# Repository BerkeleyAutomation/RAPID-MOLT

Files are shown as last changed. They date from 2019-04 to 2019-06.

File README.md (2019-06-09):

## RAPID-MOLT: A Meso-scale, Open-source, Low-cost Testbed for Robot Assisted Precision Irrigation and Delivery

To study the automation of plant-level precision irrigation, we present a modular, open-source testbed that enables real-time, fine-grained data collection and irrigation actuation. RAPID-MOLT costs USD $610 and is sized to fit a small laboratory floor space of 0.37 m^2. The functionality of the platform is evaluated by measuring the correlation between plant growth (Leaf Area Index) and water stress (Crop Water Stress Index) with irrigation volume. In line with biological studies, the observed plant growth is positively correlated with irrigation volume while water stress is negatively correlated. This testbed is the basis for ongoing work on learning-based irrigation controllers. 

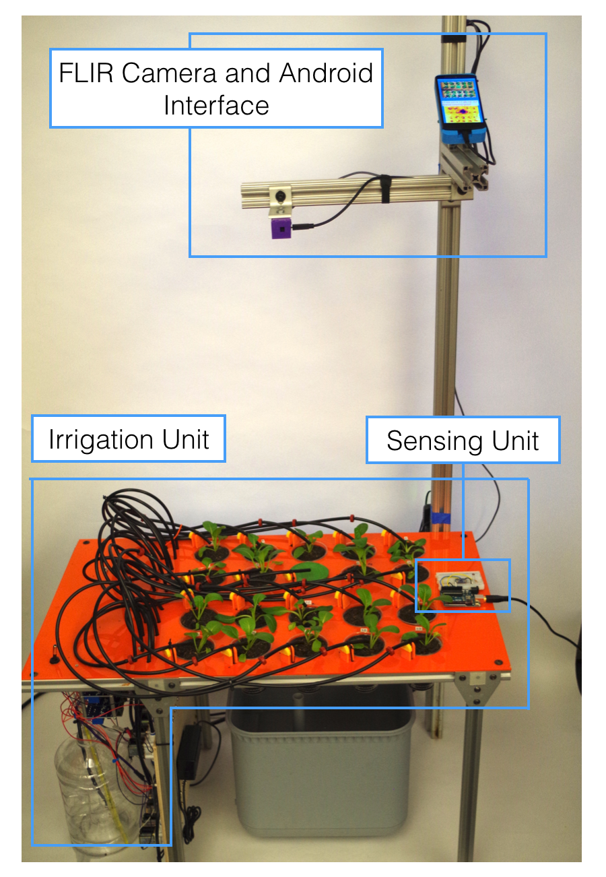
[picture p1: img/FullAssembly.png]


## Platform Basics
The contributions are as follows:
1. A hardware system design that enables both plant level sensing with multispectral imaging and also precise irrigation control with Raspberry Pi actuated solenoids.
2. A software infrastructure and data processing pipeline to evaluate irrigation controllers, including the automatic extraction of Leaf Area Index and Crop Water Stress Index from RGB and thermal images.
3. Experimental data from two experiments with different crops, reflecting plant growth and water stress data in response to different irrigation schedules.

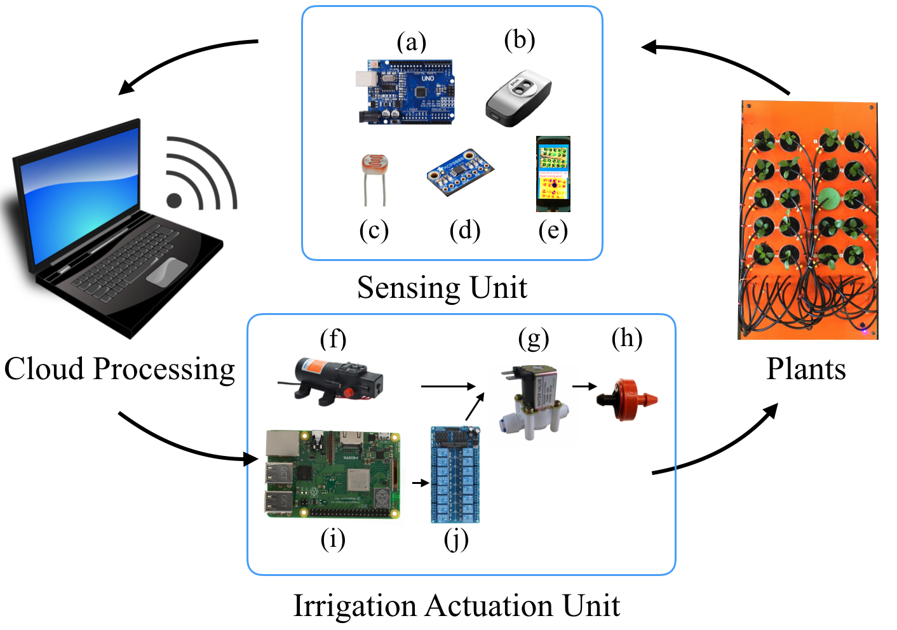
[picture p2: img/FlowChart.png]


As seen in the flow chart above, each platform unit functions together as follows. Plant and environmental images and data are collected by the sensing unit, and sent to the cloud processing unit for the creation of data-specific irrigation schedules. These schedules are relayed to the irrigation unit for irrigation deployment to the potted plants.

## Software

The software is grouped in 1) sensing, 2) data processing, and 3) actuation. 
1) The sensing folder contains the code for the android app (uploades the thermal and rgb images to the cloud) and the arduino uno. 
2) The data processing contains two core files:
- downloadImagesFromGoogleDrive.py    downloads the images from the cloud to the local computer
- process_images.py                   extracts the LAI and leaf temperature out of the images
3) The actuation folder contains the scripts and files for the raspberry pie to execute the derived irrigation schedule.

The Data folder contains an example of images from one experiment and the files resulting from the image processing.

## Hardware
CAD models for construction can be found on this repository. Code for the software infrastructure and experimental data will be posted soon.

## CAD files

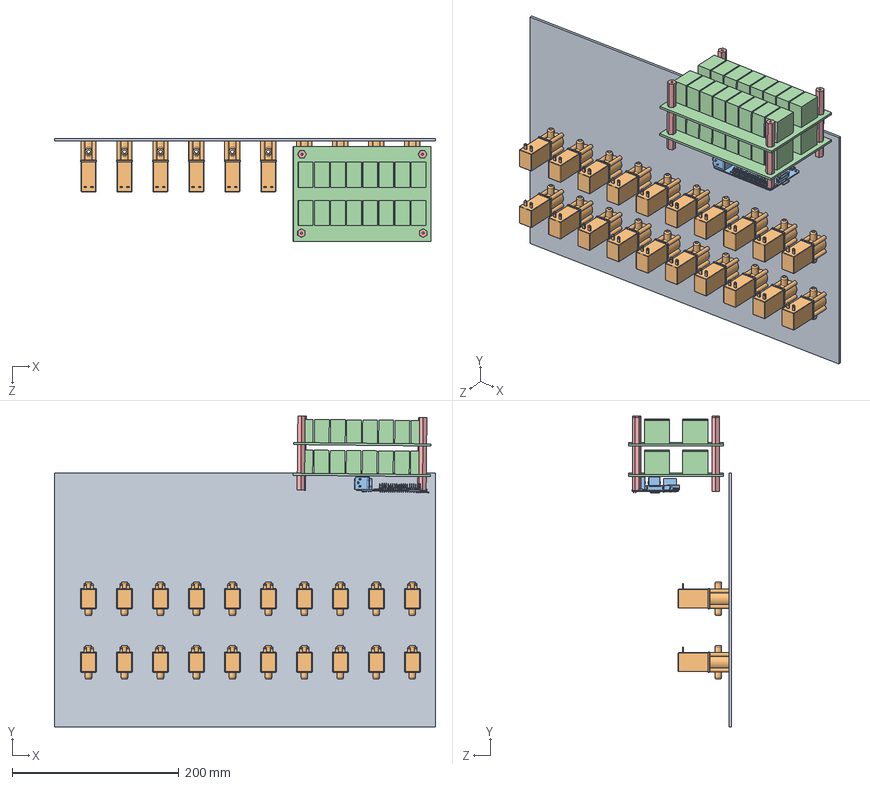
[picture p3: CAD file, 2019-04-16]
CAD/Sample Side Mount Assembly for Fusion.SLDASM
457.2 x 373.0 x 123.8 mm
Side Mount Plate
solenoid x 20
Raspberry Pi 3 Light Version
Relay_16 x 2
hex_bars x 4

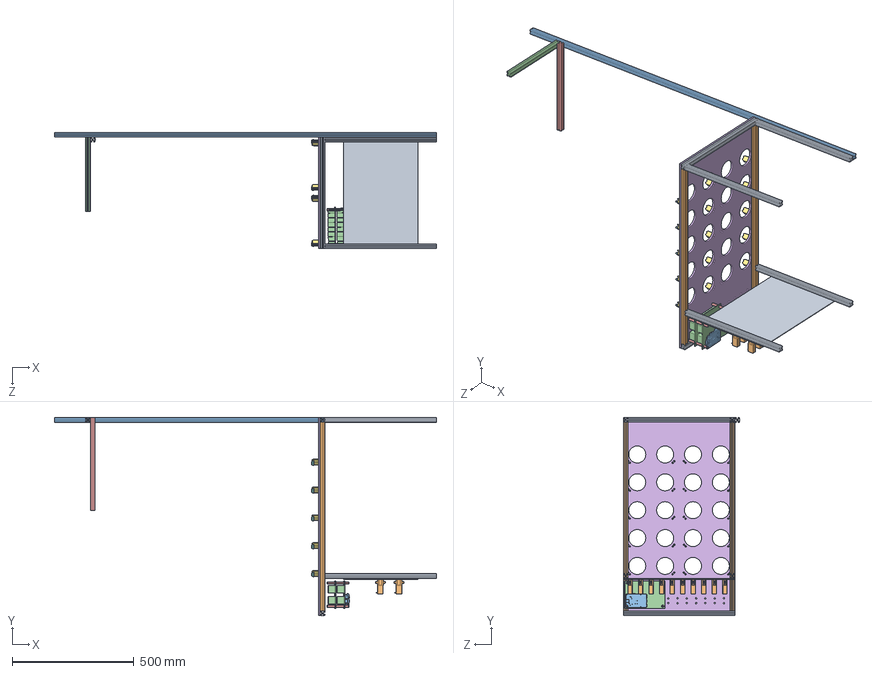
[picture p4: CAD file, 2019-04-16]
CAD/testbed_assem_3_13.SLDASM
1567.2 x 813.7 x 477.2 mm
20_2020_457_2_CL x 6
773.68_v3 x 2
1567.18_Mount8020
12in_mount
15in_Mount
top_plate
tube support x 20
add on 4 x 20
Side Mount Plate
solenoid x 20
Raspberry Pi 3 Light Version
Relay_16 x 2
hex_bars x 4

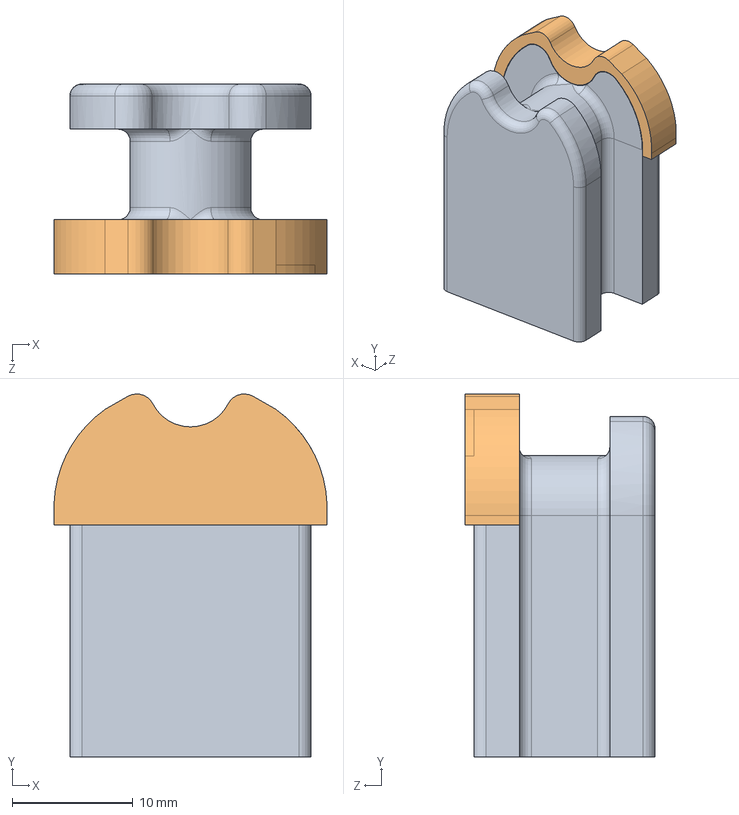
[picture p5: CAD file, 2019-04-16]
CAD/raiser assembly 2.SLDASM
22.6 x 30.1 x 15.8 mm
tube support
add on 4

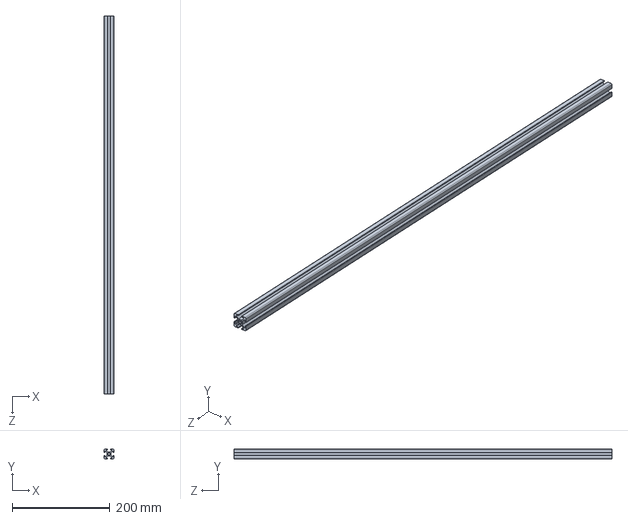
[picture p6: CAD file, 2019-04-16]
CAD/773.68_v3.SLDPRT
20.0 x 20.0 x 773.7 mm

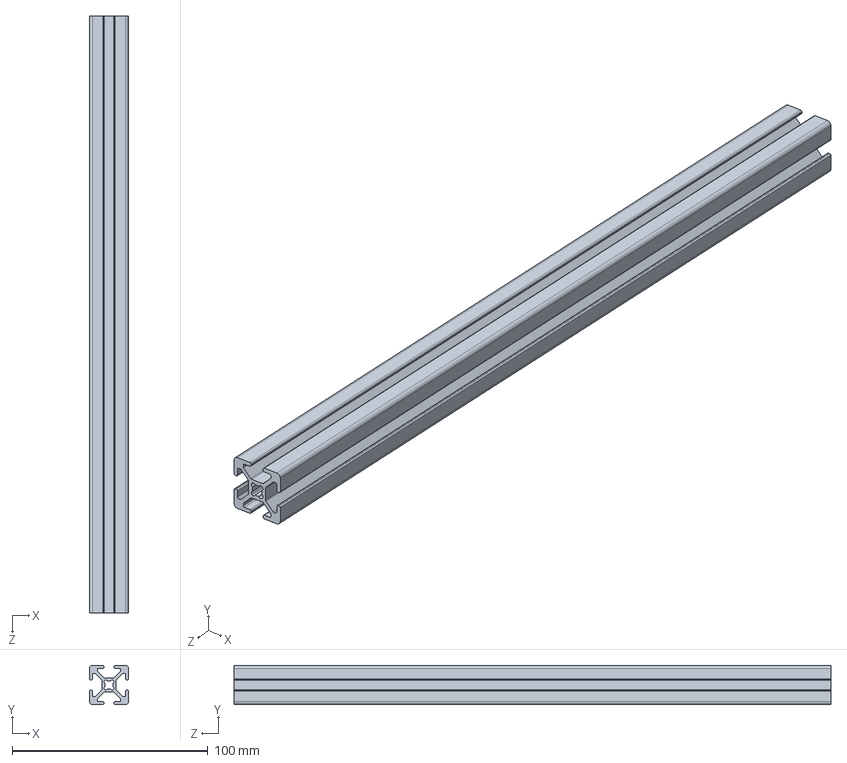
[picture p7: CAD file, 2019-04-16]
CAD/12in_mount.SLDPRT
20.0 x 20.0 x 304.8 mm

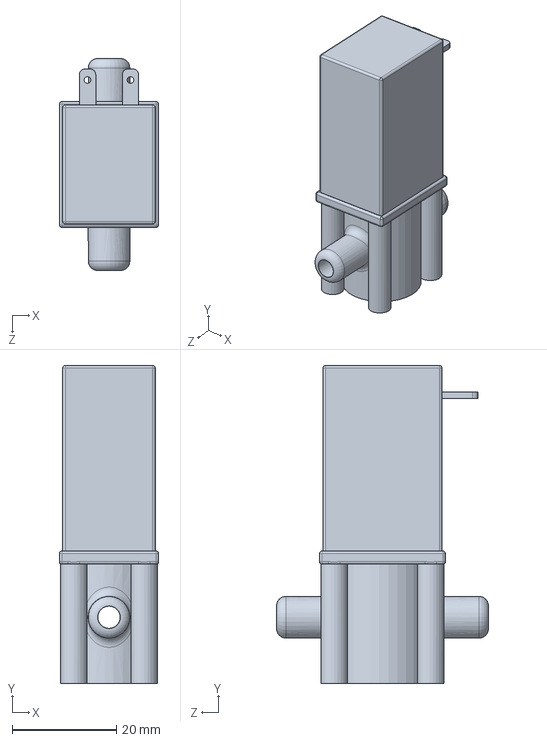
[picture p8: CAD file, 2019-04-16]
CAD/solenoid.SLDPRT
19.1 x 61.0 x 40.6 mm

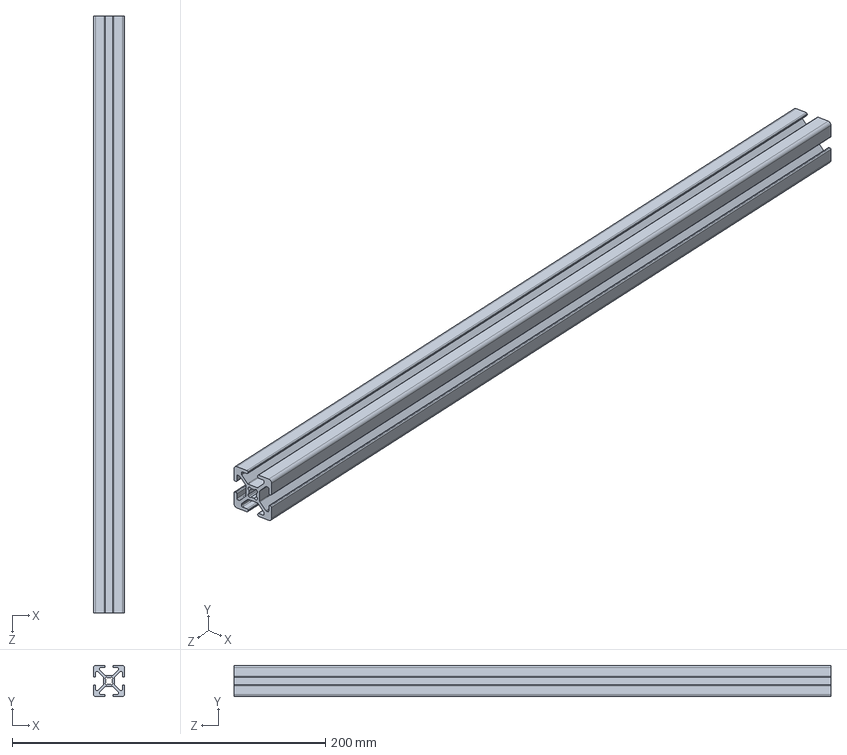
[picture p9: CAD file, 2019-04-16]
CAD/15in_Mount.SLDPRT
20.0 x 20.0 x 381.0 mm

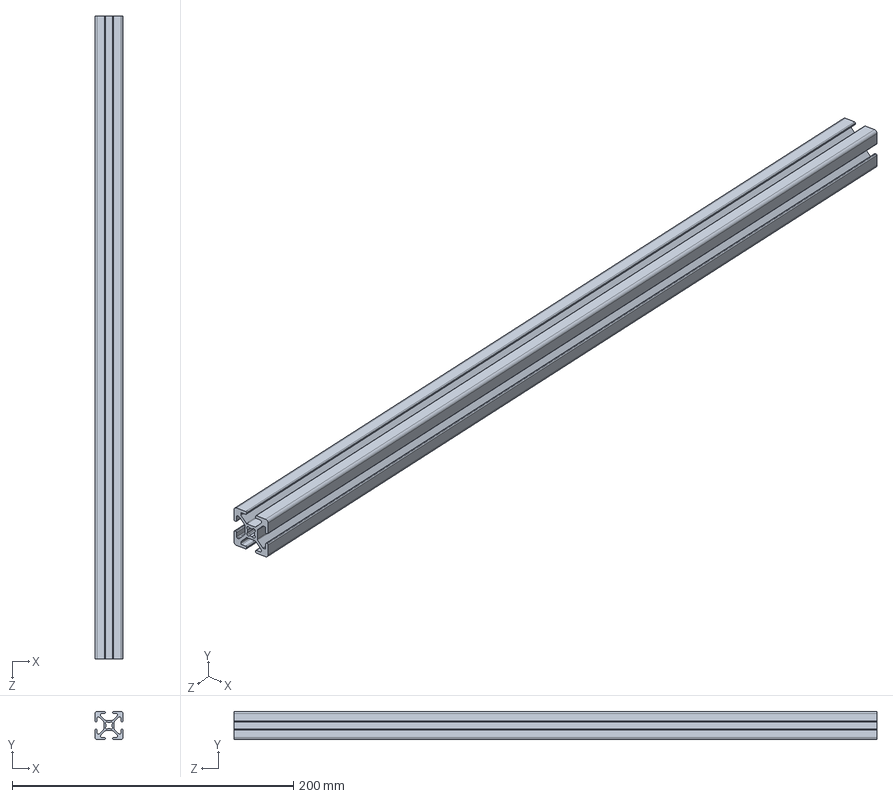
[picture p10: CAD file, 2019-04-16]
CAD/20_2020_457_2_CL.sldprt
20.0 x 20.0 x 457.2 mm

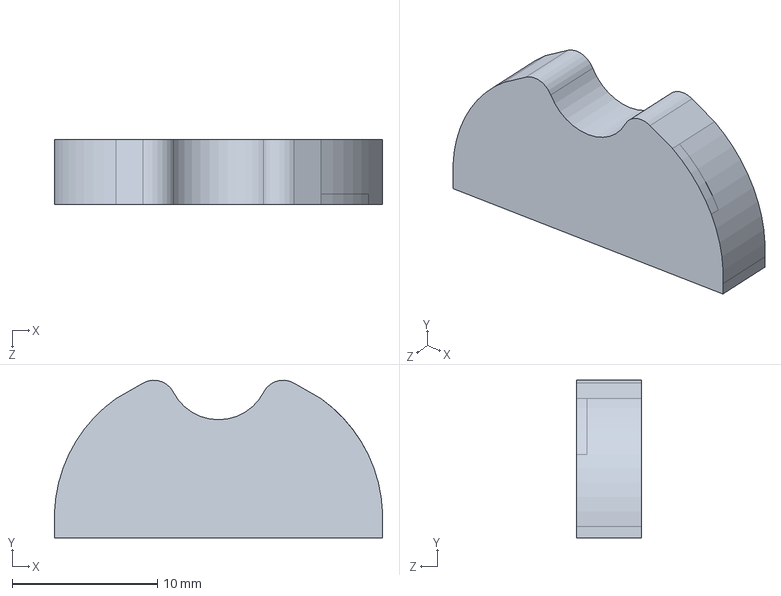
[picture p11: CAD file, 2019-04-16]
CAD/add on 4.SLDPRT
22.6 x 10.9 x 4.50 mm

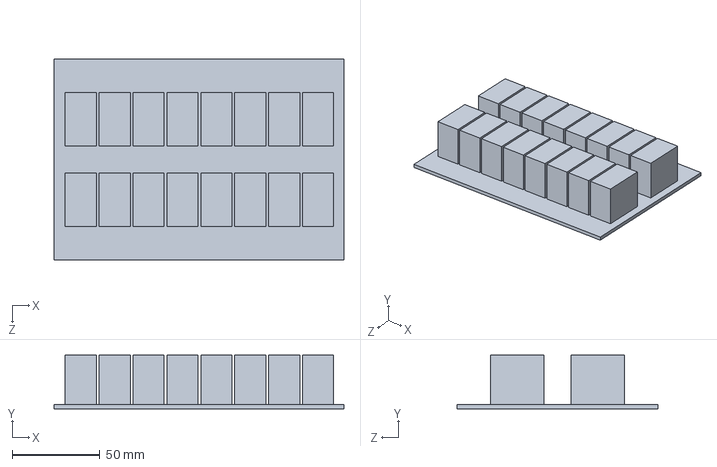
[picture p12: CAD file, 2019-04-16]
CAD/Relay_16.SLDPRT
165.1 x 30.5 x 114.3 mm

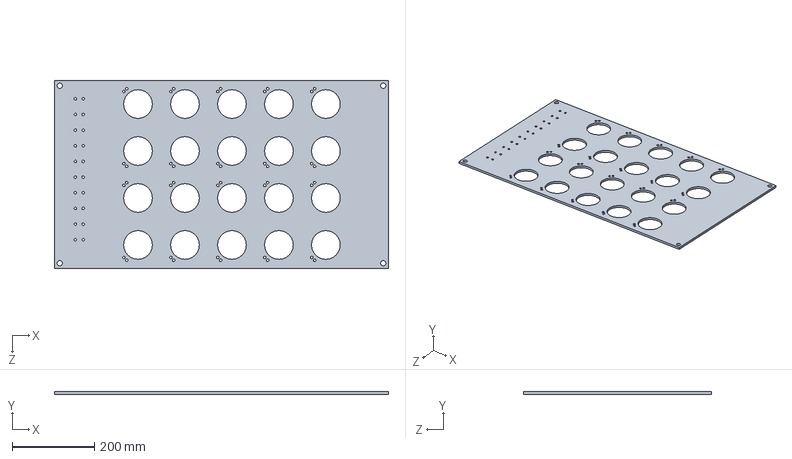
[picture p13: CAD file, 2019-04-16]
CAD/top_plate.SLDPRT
812.8 x 6.35 x 457.2 mm

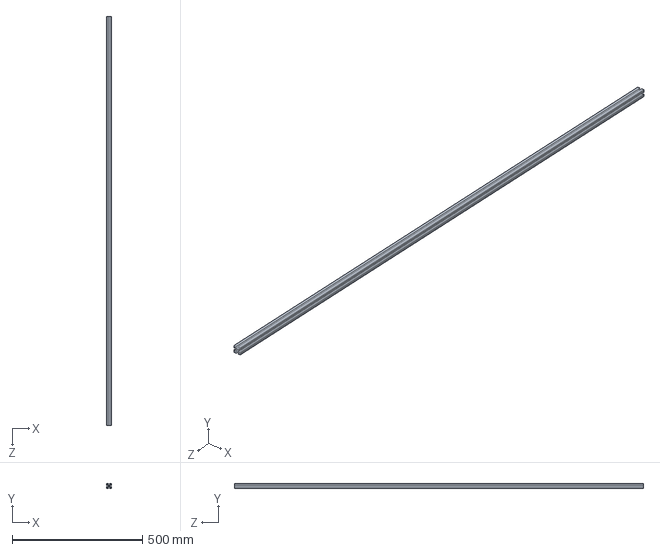
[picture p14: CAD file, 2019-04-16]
CAD/1567.18_Mount8020.SLDPRT
20.0 x 20.0 x 1567.2 mm

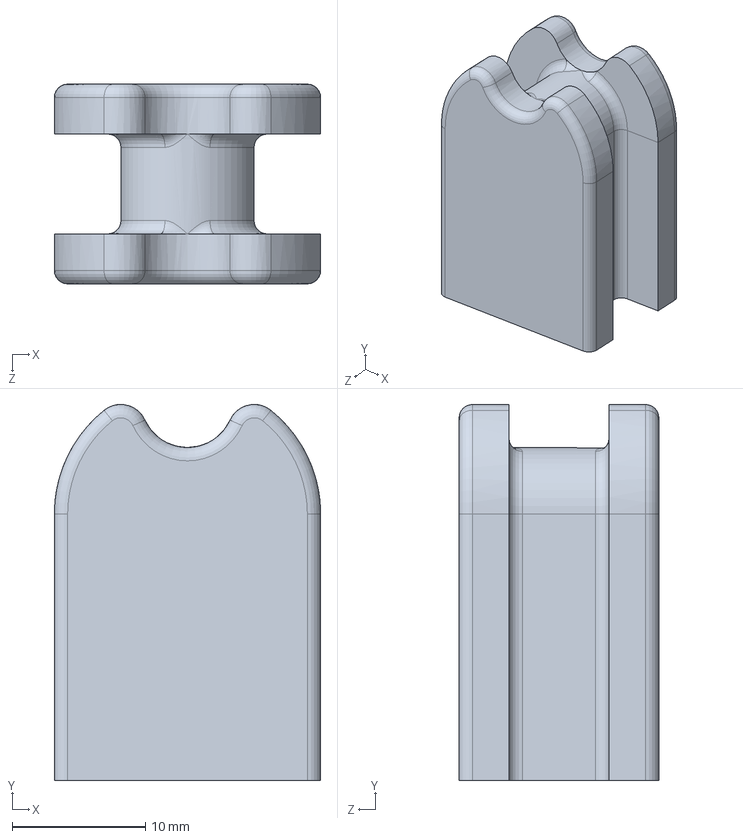
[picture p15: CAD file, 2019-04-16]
CAD/tube support.SLDPRT
20.0 x 28.2 x 15.0 mm

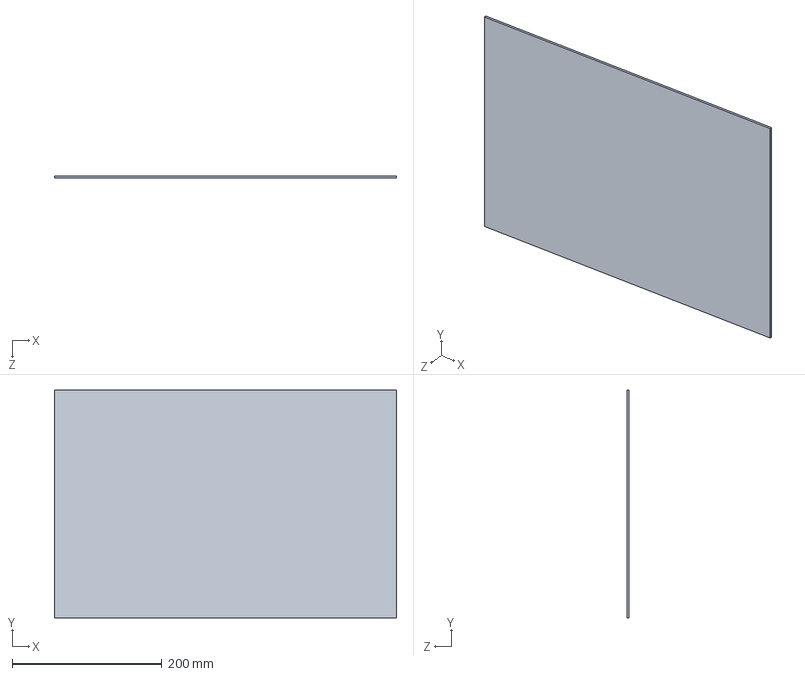
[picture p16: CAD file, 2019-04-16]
CAD/Side Mount Plate.SLDPRT
457.2 x 304.8 x 3.17 mm

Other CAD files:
CAD/hex_bars.SLDPRT

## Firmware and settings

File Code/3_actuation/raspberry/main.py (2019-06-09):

'''
This is the main script, running on the raspberry pie to control the irrigation actuation via the solenoids.

It reads from:
- emitterPinout.csv
- irrigationSchedule.csv

Format in irrigation Schedule.csv:
<pinout>, <hour>, <minute>, <second>, irrigated today (1 is yes, 0 is no)

The script logs every opening of a solenoid to: irrigationLog.txt
'''

import csv
import numpy as np
from time import sleep
import datetime
import RPi.GPIO as GPIO

irrigationSchedule = np.zeros((20, 5))
GPIO_pinout = np.zeros((20, 2))
killAll = False

# path where the irrigation log is saved
path = '/home/pi/Desktop/'
desktop_path = '/home/pi/Desktop/'
# path to the irrigation file
irrigation_file = 'irrigationSchedule.csv'

# settings for the Wet Area Reference Surface:
# Port:
wet_cloth_pot = 12
# the rate after which it should be irrigated in minutes
wet_cloth_rate = 30

GPIO.setwarnings(False)
GPIO.setmode(GPIO.BOARD)


def OnShutdown():
    global killAll
    killAll = True


def openEmitter(emitterNum, duration):
    # GPIO pin 40 is the water pump
    global GPIO_pinout
    GPIO.setup(40, GPIO.OUT)
    sleep(1)
    GPIO.output(40, GPIO.LOW)

    GPIO.setup(int(GPIO_pinout[emitterNum, 1]), GPIO.OUT)
    print('emitter number ', str(emitterNum), ' is open')
    GPIO.output(int(GPIO_pinout[emitterNum, 1]), GPIO.LOW)
    sleep(duration)
    GPIO.output(int(GPIO_pinout[emitterNum, 1]), GPIO.HIGH)

    GPIO.output(40, GPIO.HIGH)
    print('emitter number ', str(emitterNum), ' is close')

    # write to log file
    f = open(desktop_path+'irrigationLog.txt', 'a+')
    date = datetime.datetime.now().date()
    time = datetime.datetime.now().time()
    f.write(str(date) + ' ' + str(time) + ' ' + 'emitter num: ' + str(emitterNum) + ' '
            + 'duration: ' + str(duration) + '\r\n')
    f.close()


def main():
    # global irrigationSchedule
    global killAll
    global GPIO_pinout
    killAll = False

    # set the current date
    date = datetime.datetime.now().date()
    previous_day = (date - datetime.timedelta(days=1)).day
    last_time_cloth_watered = datetime.datetime.now() - datetime.timedelta(minutes=30)
    
    # read and update pinout
    from_txt = np.genfromtxt(path+'emitterPinout.csv', delimiter=',')
    for row in range(0, 20, 1):
        for col in range(0, 2, 1):
            GPIO_pinout[row, col] = int(from_txt[row, col])
    
    # closing all emitter
    for i in range(0, 20 ,1):
       GPIO.setup(int(GPIO_pinout[i, 1]), GPIO.OUT)
       GPIO.output(int(GPIO_pinout[i, 1]), GPIO.HIGH)
    sleep(2)

    # constant loop
    while ~killAll:
        # update irrigationSchedule
        from_txt = np.genfromtxt(path+irrigation_file, delimiter=',')
        for row in range(0, 20, 1):
            for col in range(0, 5, 1):
                irrigationSchedule[row, col] = from_txt[row, col]

        # check if the day changed, if yes updated irrigation status
        date = datetime.datetime.now().date()
        if date.day != previous_day:
            print('day changed, initializing irrigation status...')
            # initializing the irrigation tracking
            for row in irrigationSchedule:
                irrigationSchedule[int(row[0]), 4] = 0
                with open(path+irrigation_file, 'wb') as cvsfile:
                    to_txt = csv.writer(cvsfile, delimiter=',')
                    for row in irrigationSchedule:
                        to_txt.writerow(row)
            previous_day = date.day

        # check if the wet cloth should be irrigated again
        if datetime.datetime.now() >= (last_time_cloth_watered + datetime.timedelta(minutes=wet_cloth_rate)):
                # set the irrigation schedule at wet cloth pot to "not irrigated"
                irrigationSchedule[wet_cloth_pot, 4] = 0
                # Write it to the CSV file
                with open(path+irrigation_file, 'wb') as cvsfile:
                    to_txt = csv.writer(cvsfile, delimiter=',')
                    for row in irrigationSchedule:
                        to_txt.writerow(row)
                # set last_time_cloth_watered to current
                last_time_cloth_watered = datetime.datetime.now()

        time_now = datetime.datetime.now().time()
        time_now_int = int(time_now.hour * 60 + time_now.minute)

        # iterate over the schedule and open corresponding emitters
        for row in irrigationSchedule:
            emitter_num = int(row[0])
            irrigation_hour = row[1]
            irrigation_minute = row[2]
            irrigation_duration = row[3]
            was_irrigated = row[4]

            # check which emitters should be open and open them
            if time_now_int > (irrigation_hour*60+irrigation_minute) and was_irrigated == 0:
                irrigationSchedule[emitter_num, 4] = 1
                with open(path + irrigation_file, 'wb') as cvsfile:
                    to_txt = csv.writer(cvsfile, delimiter=',')
                    for row in irrigationSchedule:
                        to_txt.writerow(row)
                openEmitter(emitter_num, irrigation_duration)

        sleep(2)

if __name__ == '__main__':
    try:
        main()
    except KeyboardInterrupt:
        OnShutdown()

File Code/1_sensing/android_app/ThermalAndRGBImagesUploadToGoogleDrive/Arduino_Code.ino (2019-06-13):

#include <Time.h>
#include <TimeLib.h>


/**************************************************************************/
/*!
Adapted from Adafruit demo of Adafruit MCP9808 breakout
----> http://www.adafruit.com/products/1782
*/
/**************************************************************************/

#include <Wire.h>
#include "Adafruit_MCP9808.h"
const int lightPin = 0;
int sensorValue = 0;
Adafruit_MCP9808 tempsensor = Adafruit_MCP9808();

void setup() {
  Serial.begin(9600);
  while (!Serial); //waits for serial terminal to be open, necessary in newer arduino boards.
  pinMode(lightPin, INPUT);
  if (!tempsensor.begin(0x18)) {
    Serial.println("Couldn't find MCP9808! Check your connections and verify the address is correct.");
    while (1);
  }
    
  tempsensor.setResolution(3); // sets the resolution mode of reading, the modes are defined in the table bellow:

}

void loop() {
  tempsensor.wake();   // wake up, ready to read!
  float c = tempsensor.readTempC();
  float f = tempsensor.readTempF(); 
  Serial.print(c, 4); Serial.print(",");//C 
  Serial.print(f, 4); Serial.print(",");//F
  Serial.print(analogRead(lightPin)); //Serial.print(" Lux"); 
  delay(2000);
  tempsensor.shutdown_wake(1); // shutdown MSP9808 - power consumption ~0.1 mikro Ampere, stops temperature sampling
  Serial.println("");
  delay(200);
}
